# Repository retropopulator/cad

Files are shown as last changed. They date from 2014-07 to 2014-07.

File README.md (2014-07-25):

# Retro Populator CAD Files: Version 1

### Build Instructions

Warning I spent only 20 minutes to create these so some in accuracies may exist 

The Iges files for retro populator

Need table saw or laser cutter for all parts
note there are both metric and imperial units.  Imperial tools & hardware, metric spacing.

#### Pinplate
This is the fixture base, can be created with either a milling machine or cnc mill. In desperation you could try a drill press.

#### Boardwall
Need 2

These rails are glued to the base plate. Can be created with a mill, cnc, or 2mm saw blade OR the 1mm woodruff cutter.

#### Railspacers
Need 4

Are screwed to the pinplate. Can be made with mill or drill press.

#### 8mm rail
Need 6 to 10

These are screwed to the rail spacers. Mill.  Will need a 1 mm woodruff cutter. I made my own. Could try 3d printing these.

#### Aarm
Need 4

Are attached to the base plate, screw or glue hand drill is fine

#### wing
Need 2

These are attached to the Aarm and a set of screws should be inserted to align to the printers base plate. this makes for the quick change out.

#### Cam locks
Need a wack of em, can be 3d printed but better to cnc with that 1mm woodruff.

1/8x.5 dowel pin is added to them.

Nozzle components comming soon

Review the videos to see where it all fits.  Assembly drawing with labels coming soon.

Good luck
updated July 24 2014

## Usage

**Note:** The useage instructions are a work in progress.

### Initial Setup (1 time)

#### 1. Position the Jig

* needle should be perfectly positioned over one of the holes
* confirming the jig orienation and alignment

#### 2. Calibrate the Z Endstop Extension

* screw the z endstop onto the z

#### 3. Install PopCAM

* See [https://github.com/retropopulator/popcam#installation-osx-and-linux](PopCAM Installation Instructions)

### Regular Setup

#### 1. Align the first circuit board

* 1.1 Insert your first circuit board at the intersection of the two board walls (the furthest corner from the alignement screws). Make sure to fit your board in the slots along each wall.
* 1.2 Insert your first camlock with the larger diameter towards the board in the hole closest to the other edge of your first circuit board.
* 1.3 Rotate the camlock to engage the circuit board, holding it in place against the board walls. Make sure your board is still in the slots on the rail and that it is in the slot on the camlock.
* 1.4 Add a second camlock to the last open side of the board, rotating it into position in the same way you did the first camlock (see 1.2 and 1.3).

**Note:** An additional camlock may be required on one of the board sides when placing multiple boards.

#### 2. Aligning the rest of the circuit boards

* 2.1 Stack additional boards against the camlocks holding previous boards.

#### 3. Insert the tapes

* Put the peg in
* While being careful not to knock components off the tape, peel the plastic cover off.
* Remove peg. Be careful not to shift the tape or knock the components off it.

#### 4. Position the jig

* Slide the jig into the 3D printer until the alignment screws are pressed against the edge of the build platform.

#### 5. Configure PopCAM

* More info comming soon. For now refer to the popcam docs.

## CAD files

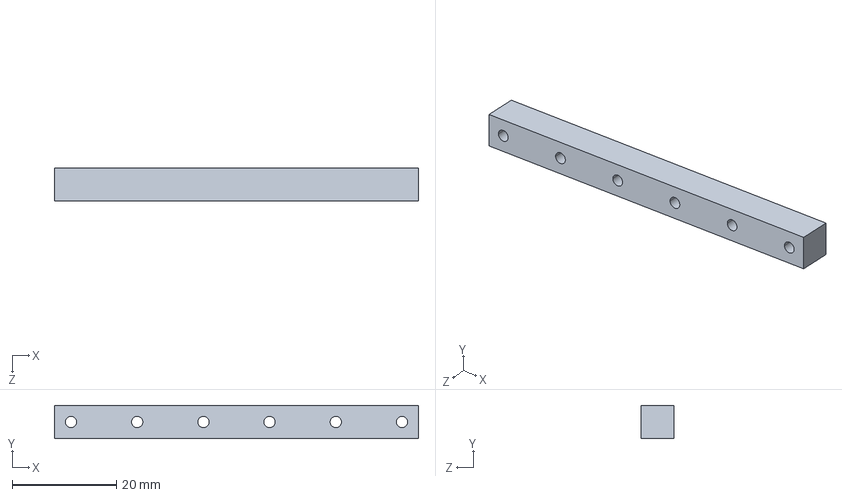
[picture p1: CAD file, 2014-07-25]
Aarm.IGS
69.8 x 6.35 x 6.35 mm

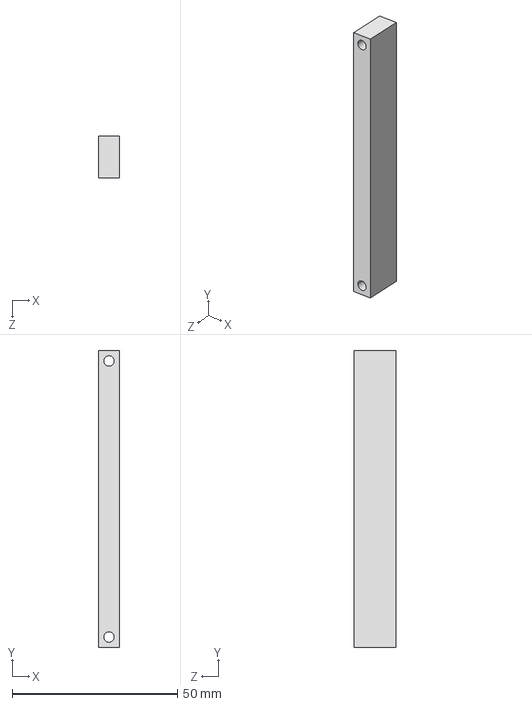
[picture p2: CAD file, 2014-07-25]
wing.IGS
6.35 x 90.0 x 12.7 mm

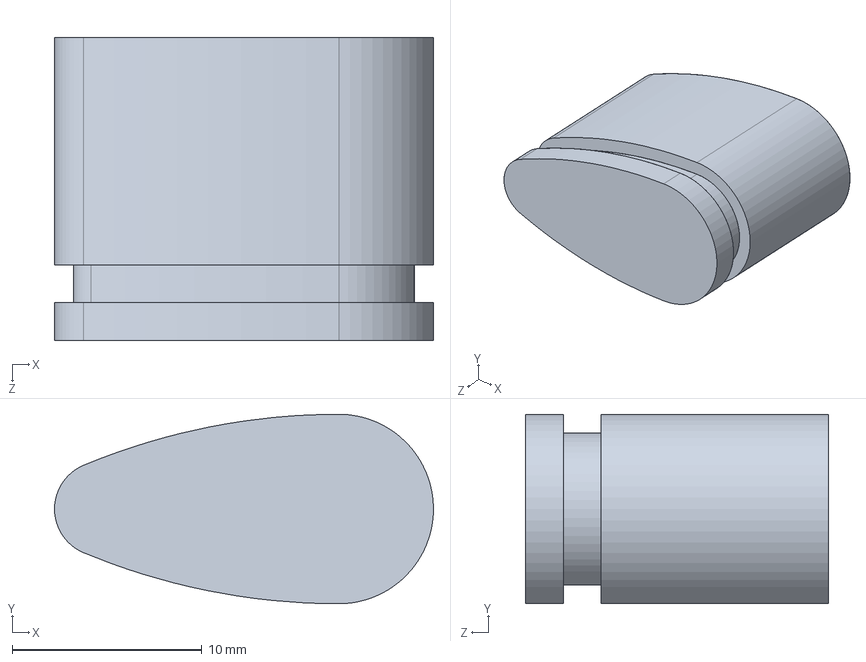
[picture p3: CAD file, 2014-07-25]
camlock.IGS
20.0 x 10.00 x 16.0 mm

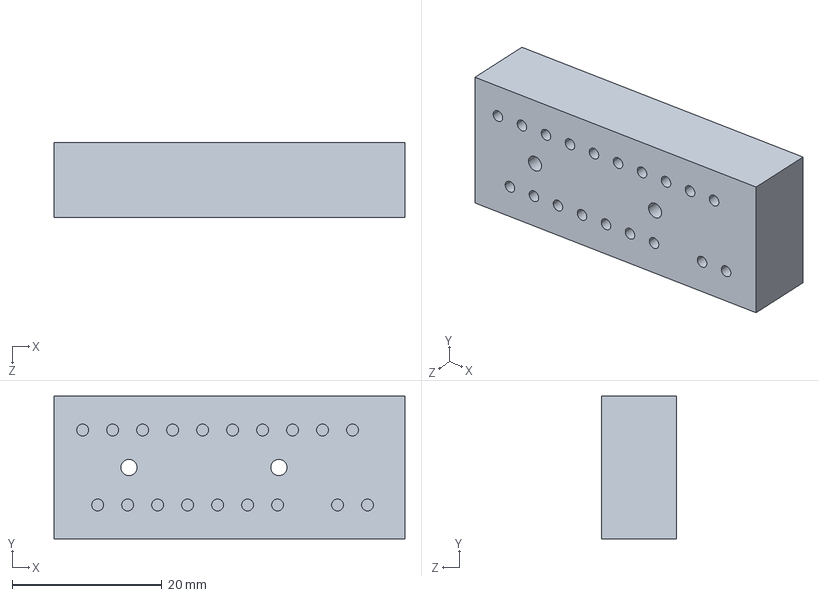
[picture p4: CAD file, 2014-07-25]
railspacer.IGS
46.8 x 19.0 x 10.0 mm

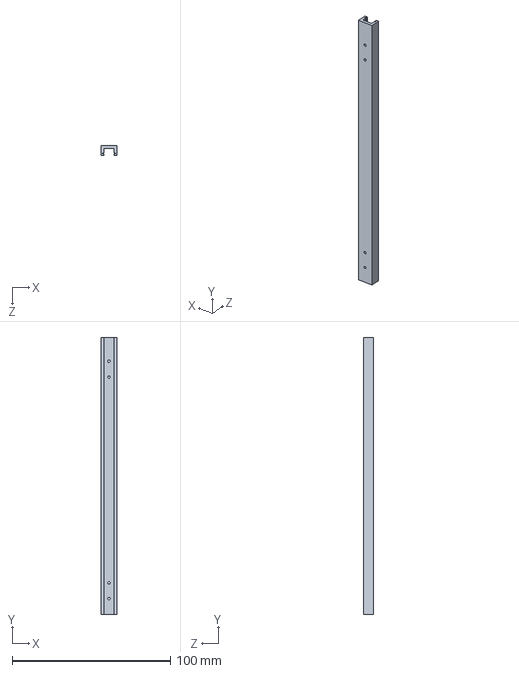
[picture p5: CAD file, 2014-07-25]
8mmRail.IGS
10.00 x 175.0 x 6.35 mm

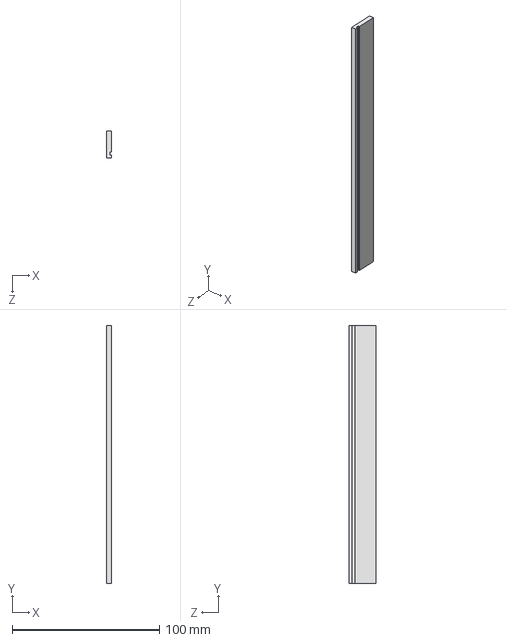
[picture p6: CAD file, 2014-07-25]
boardwall.IGS
3.17 x 175.0 x 18.0 mm
